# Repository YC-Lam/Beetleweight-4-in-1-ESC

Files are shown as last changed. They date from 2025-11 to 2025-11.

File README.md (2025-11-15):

# beetleweight 4 in 1 brushless ESC
 a 4 in 1 ESC designed for UK beetleweight robots. It can power two brushless drive and one weapon motor.

## Features
- Two 20A brushless drive motor
- Single 80A brushless weapon motor
- Integrated fuse to accommodate BBB rules
- On-board gyroscope to invert controls when bot is inverted (optional)
- On-board BLE reciever to control bot over an XBox controller
- Supports 2-6s Lipo battery
- configurable UVLO, OVP and OCP
- Compact with a 50x50mm dimension
- Single side SMD soldering for easy manufaturing (some hand soldered resistors at the back)

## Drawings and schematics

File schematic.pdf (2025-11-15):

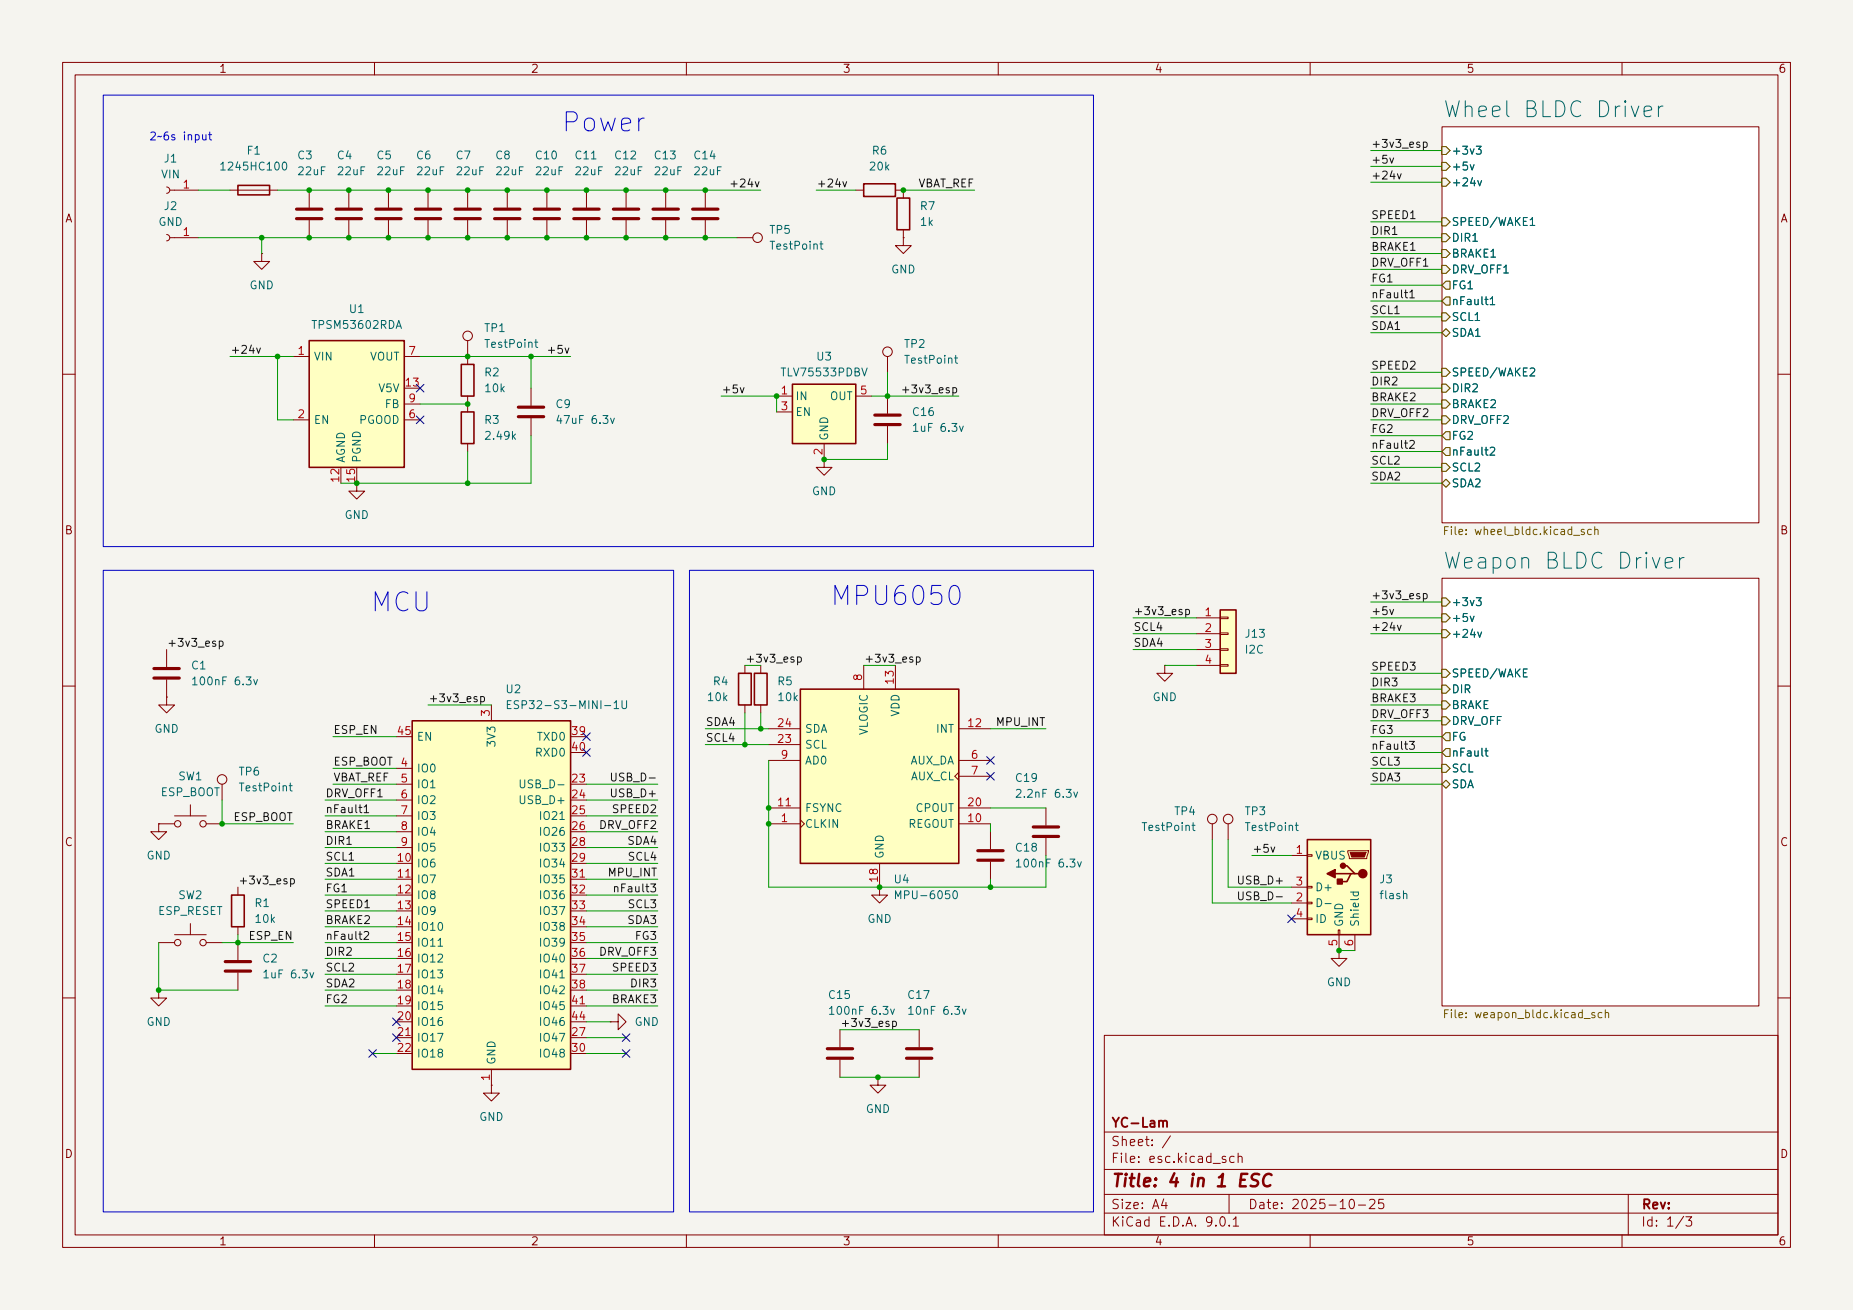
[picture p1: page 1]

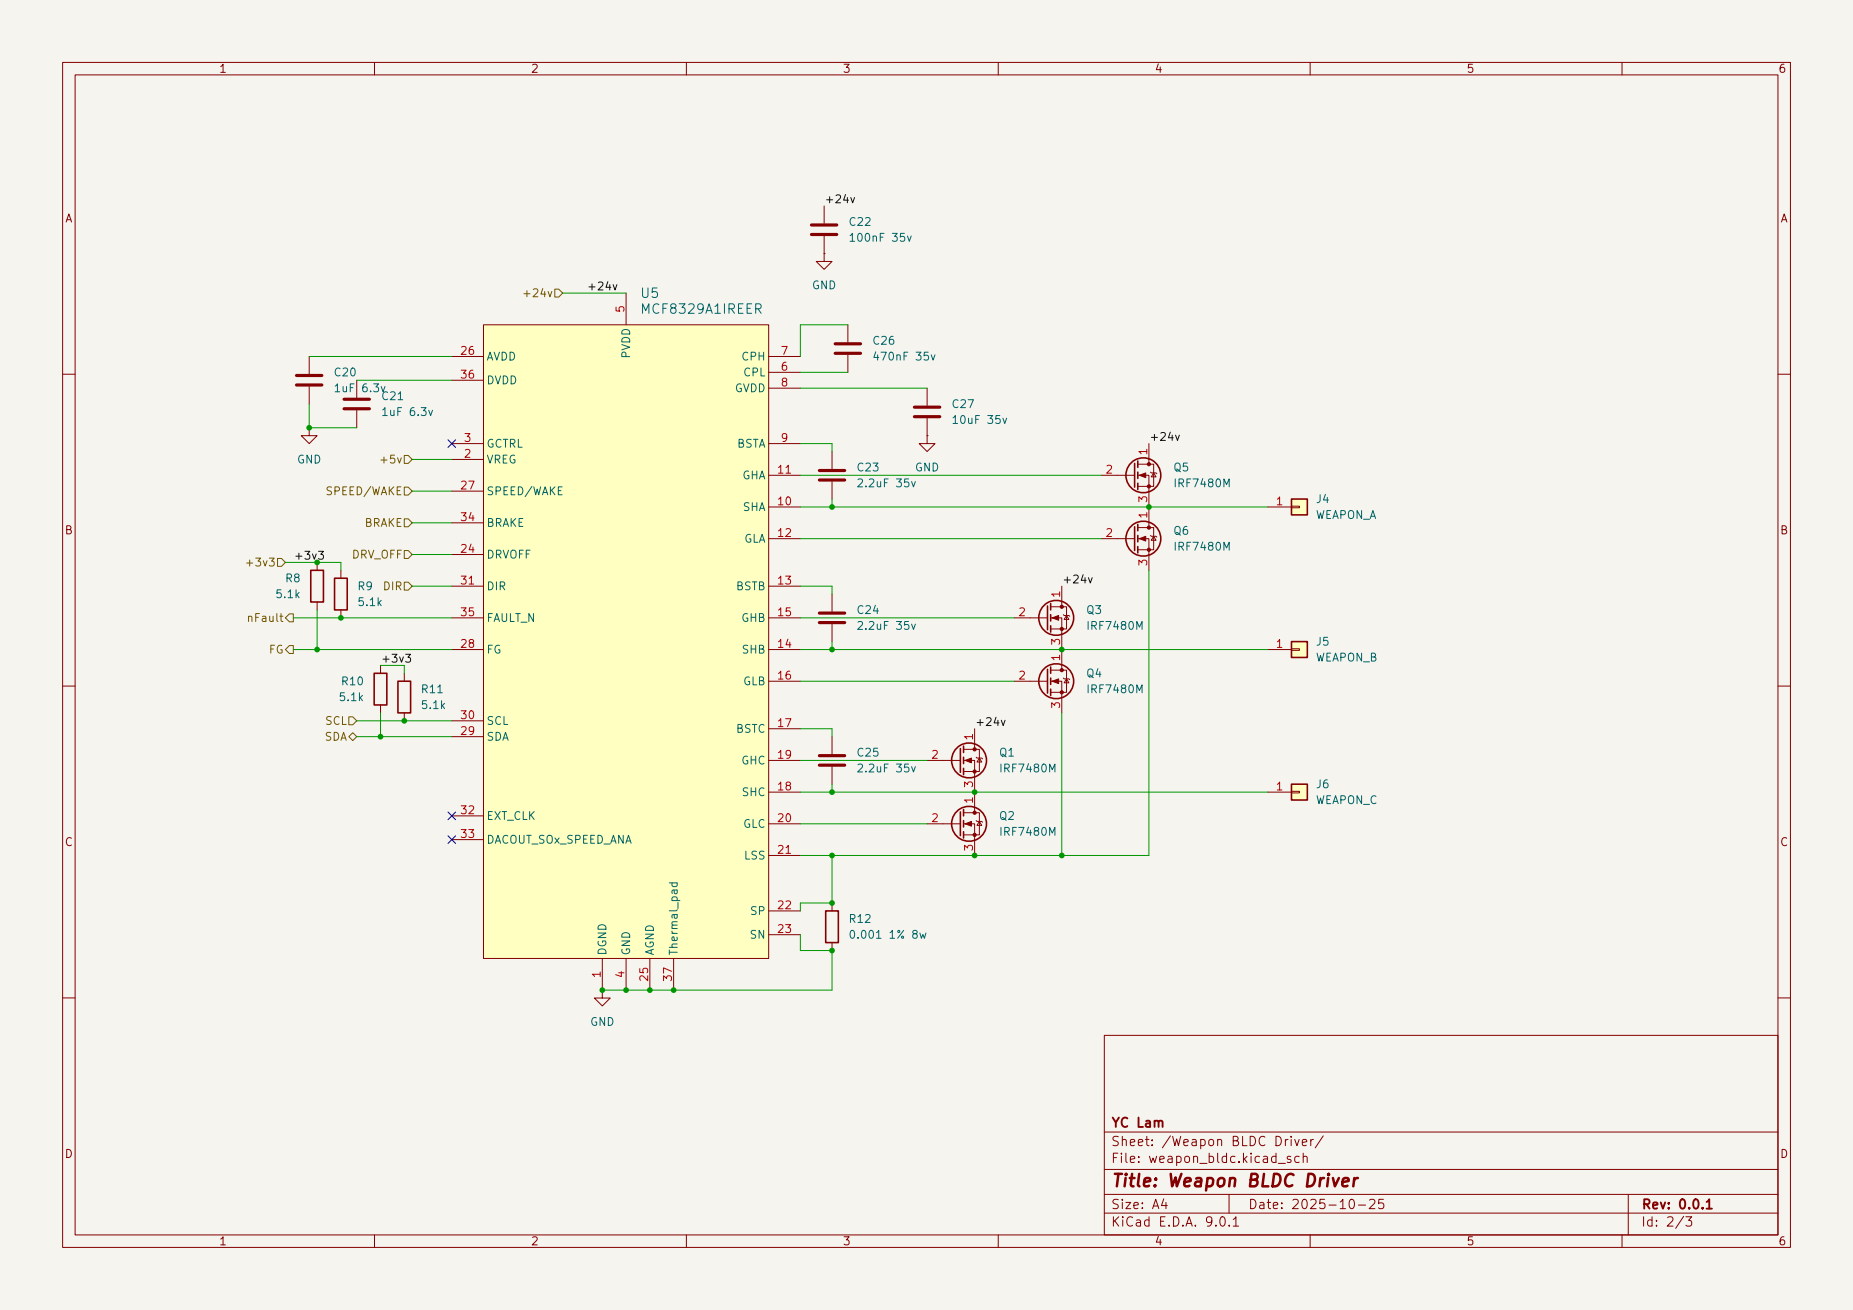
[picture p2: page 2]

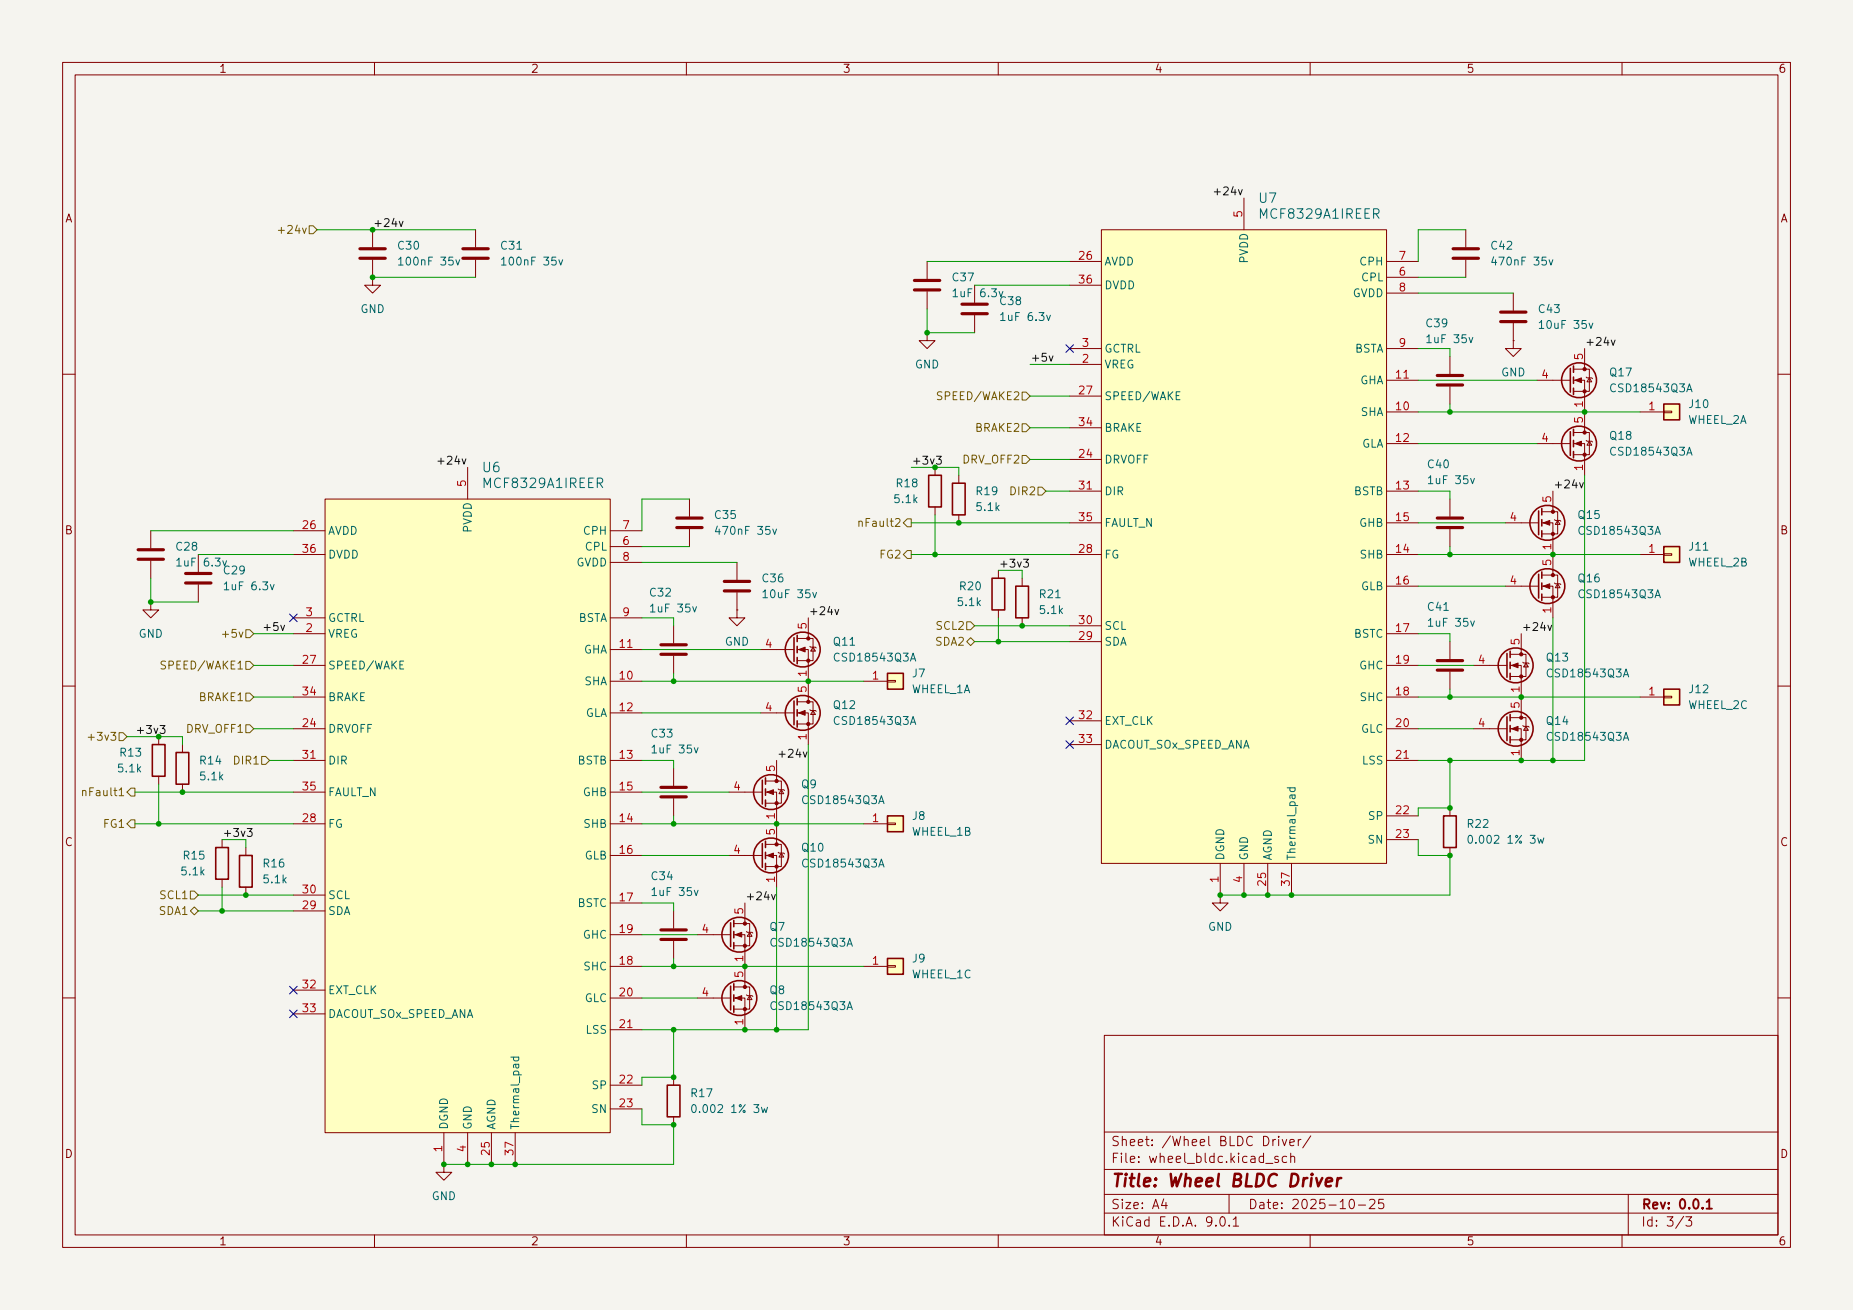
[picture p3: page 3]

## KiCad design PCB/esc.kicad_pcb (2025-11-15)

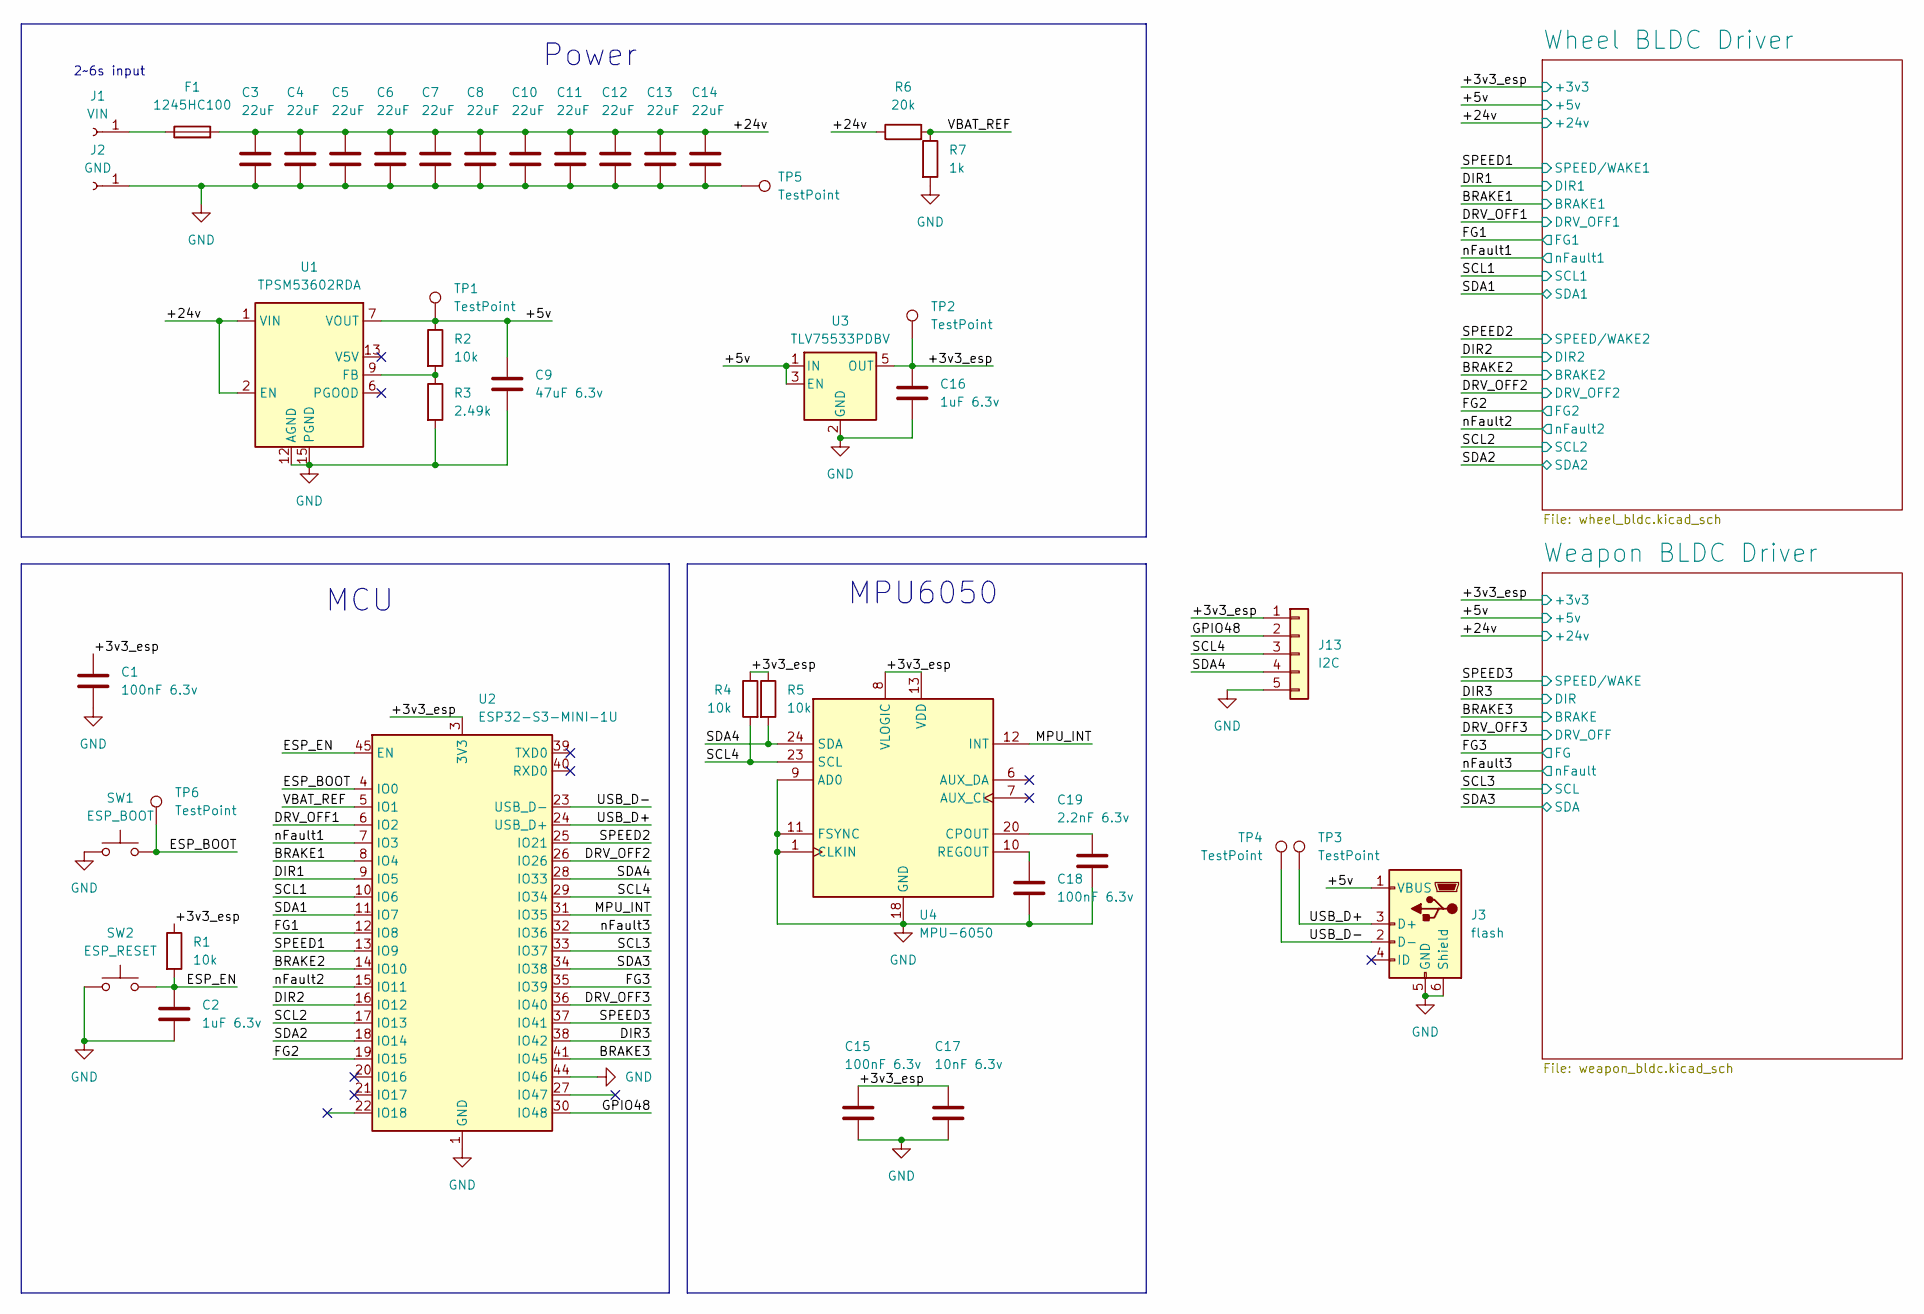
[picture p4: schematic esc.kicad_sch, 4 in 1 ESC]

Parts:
C1, C15, C18: 100nF 6.3v; C_0402_1005Metric
C2: 1uF 6.3v; C_0603_1608Metric_Pad1.08x0.95mm_HandSolder
C3, C4, C5, C6, C7, C8, C10, C11, C12, C13, C14: 22uF; C_0805_2012Metric
C9: 47uF 6.3v; C_0603_1608Metric
C16: 1uF 6.3v; C_0402_1005Metric
C17: 10nF 6.3v; C_0402_1005Metric
C19: 2.2nF 6.3v; C_0402_1005Metric
F1: 1245HC100; 1245HC
J1: VIN; WIRE
J2: GND; WIRE
J3: flash; USB_Micro-B_Molex_47346-0001
J13: I2C; signal wire
R1: 10k; R_0603_1608Metric_Pad0.98x0.95mm_HandSolder
R2, R4, R5: 10k; R_0402_1005Metric
R3: 2.49k; R_0402_1005Metric
R6: 20k; R_0402_1005Metric
R7: 1k; R_0402_1005Metric
SW1: ESP_BOOT; SW_SPST_B3U-1000P
SW2: ESP_RESET; SW_SPST_B3U-1000P
TP1, TP2, TP3, TP4, TP5, TP6: TestPoint; TestPoint_Pad_D1.0mm
U1: TPSM53602RDA; Texas_B3QFN-14-1EP_5x5.5mm_P0.65mm
U2: ESP32-S3-MINI-1U; ESP32-S2-MINI-1U
U3: TLV75533PDBV; SOT-23-5
U4: MPU-6050; InvenSense_QFN-24_4x4mm_P0.5mm

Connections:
/+3v3_esp: C1.1, C15.1, C16.1, C17.1, J13.1, R1.1, R4.1, R5.1, TP2.1, U2.3 (3V3), U3.5 (OUT), U4.8 (VLOGIC), U4.13 (VDD); also elsewhere on the board
/+5v: C9.1, J3.1 (VBUS), R2.1, TP1.1, U1.7 (VOUT), U1.8 (VOUT), U3.1 (IN), U3.3 (EN); also elsewhere on the board
/+24v: C3.1, C4.1, C5.1, C6.1, C7.1, C8.1, C10.1, C11.1, C12.1, C13.1, C14.1, F1.2, R6.1, U1.1 (VIN), U1.2 (EN), U1.14 (VIN); also elsewhere on the board
/BRAKE1: U2.8 (IO4); also elsewhere on the board
/BRAKE2: U2.14 (IO10); also elsewhere on the board
/BRAKE3: U2.41 (IO45); also elsewhere on the board
/DIR1: U2.9 (IO5); also elsewhere on the board
/DIR2: U2.16 (IO12); also elsewhere on the board
/DIR3: U2.38 (IO42); also elsewhere on the board
/DRV_OFF1: U2.6 (IO2); also elsewhere on the board
/DRV_OFF2: U2.26 (IO26); also elsewhere on the board
/DRV_OFF3: U2.36 (IO40); also elsewhere on the board
/ESP_BOOT: SW1.2, TP6.1, U2.4 (IO0)
/ESP_EN: C2.1, R1.2, SW2.2, U2.45 (EN)
/FG1: U2.12 (IO8); also elsewhere on the board
/FG2: U2.19 (IO15); also elsewhere on the board
/FG3: U2.35 (IO39); also elsewhere on the board
/GPIO48: J13.2, U2.30 (IO48)
/MPU_INT: U2.31 (IO35), U4.12 (INT)
/SCL1: U2.10 (IO6); also elsewhere on the board
/SCL2: U2.17 (IO13); also elsewhere on the board
/SCL3: U2.33 (IO37); also elsewhere on the board
/SCL4: J13.3, R4.2, U2.29 (IO34), U4.23 (SCL)
/SDA1: U2.11 (IO7); also elsewhere on the board
/SDA2: U2.18 (IO14); also elsewhere on the board
/SDA3: U2.34 (IO38); also elsewhere on the board
/SDA4: J13.4, R5.2, U2.28 (IO33), U4.24 (SDA)
/SPEED1: U2.13 (IO9); also elsewhere on the board
/SPEED2: U2.25 (IO21); also elsewhere on the board
/SPEED3: U2.37 (IO41); also elsewhere on the board
/USB_D+: J3.3 (D+), TP3.1, U2.24 (USB_D+)
/USB_D-: J3.2 (D-), TP4.1, U2.23 (USB_D-)
/VBAT_REF: R6.2, R7.1, U2.5 (IO1)
/nFault1: U2.7 (IO3); also elsewhere on the board
/nFault2: U2.15 (IO11); also elsewhere on the board
/nFault3: U2.32 (IO36); also elsewhere on the board
GND: C1.2, C2.2, C3.2, C4.2, C5.2, C6.2, C7.2, C8.2, C9.2, C10.2, C11.2, C12.2, C13.2, C14.2, C15.2, C16.2, C17.2, C18.2, C19.2, J2.1, J3.5 (GND), J3.6 (Shield), J13.5, R3.2, R7.2, SW1.1, SW2.1, TP5.1, U1.3 (PGND), U1.10 (PGND), U1.11 (PGND), U1.12 (AGND), U1.15 (PGND), U2.1 (GND), U2.2 (GND), U2.42 (GND), U2.43 (GND), U2.44 (IO46), U2.46 (GND), U2.47 (GND), U2.48 (GND), U2.49 (GND), U2.50 (GND), U2.51 (GND), U2.52 (GND), U2.53 (GND), U2.54 (GND), U2.55 (GND), U2.56 (GND), U2.57 (GND), U2.58 (GND), U2.59 (GND), U2.60 (GND), U2.61 (GND), U2.62 (GND), U2.63 (GND), U2.64 (GND), U2.65 (GND), U3.2 (GND), U4.1 (CLKIN), U4.9 (AD0), U4.11 (FSYNC), U4.18 (GND); also elsewhere on the board
unnamed: F1.1, J1.1
unnamed: R2.2, R3.1, U1.9 (FB)
unnamed: C19.1, U4.20 (CPOUT)
unnamed: C18.1, U4.10 (REGOUT)

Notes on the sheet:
MPU6050
Power
2~6s input
MCU

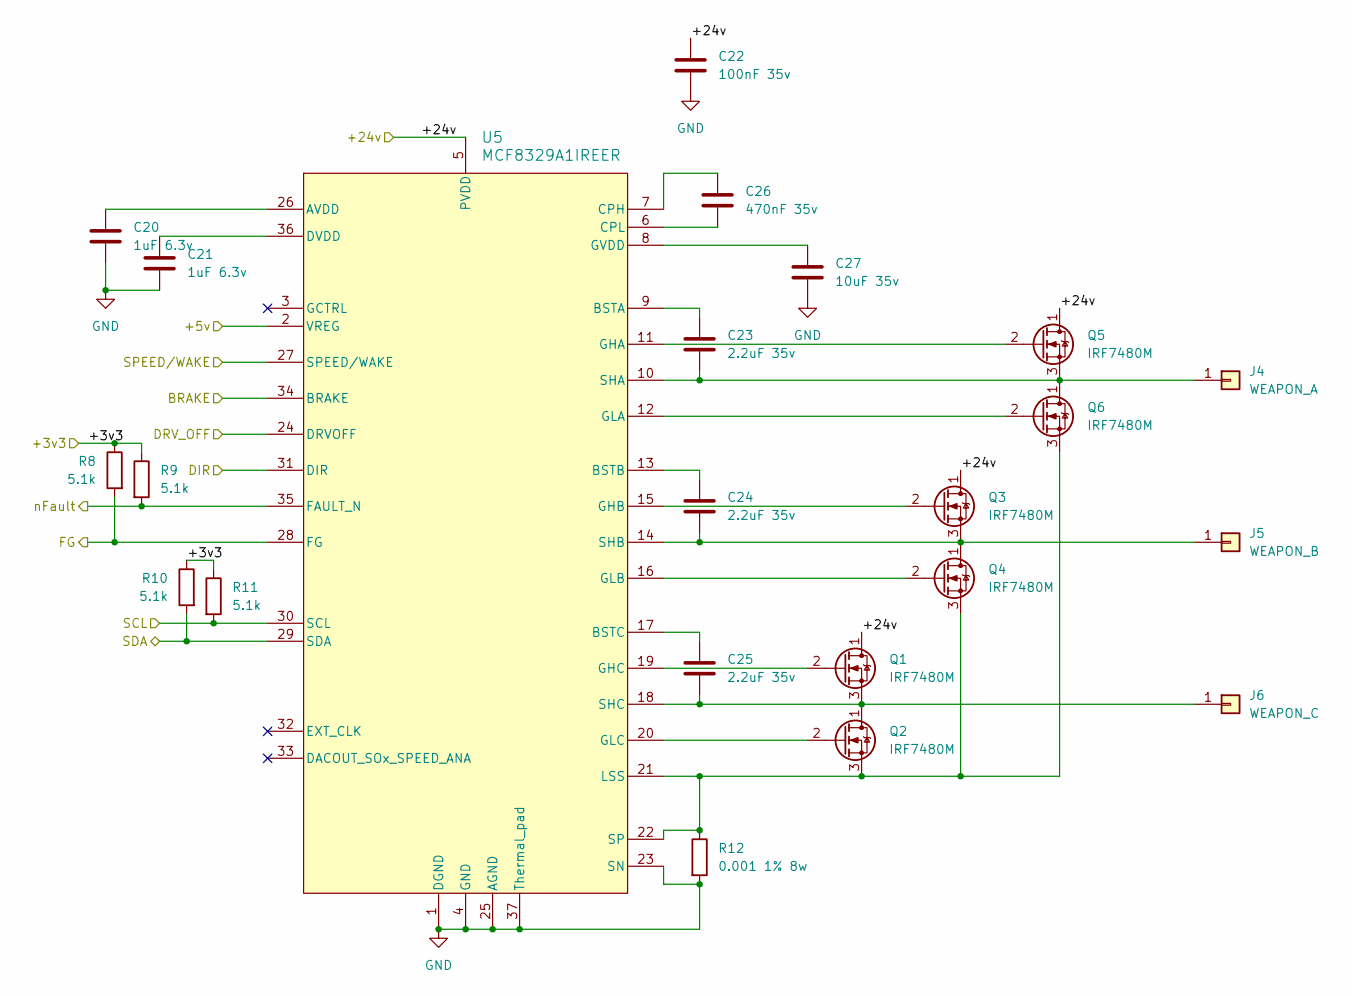
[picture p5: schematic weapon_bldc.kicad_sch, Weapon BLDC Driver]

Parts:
C20, C21: 1uF 6.3v; C_0402_1005Metric
C22: 100nF 35v; C_0402_1005Metric
C23, C24, C25: 2.2uF 35v; C_0402_1005Metric
C26: 470nF 35v; C_0402_1005Metric
C27: 10uF 35v; C_0603_1608Metric
J4: WEAPON_A; WIRE
J5: WEAPON_B; WIRE
J6: WEAPON_C; WIRE
Q1, Q2, Q3, Q4, Q5, Q6: IRF7480M; DirectFET_ME
R8, R9, R10, R11: 5.1k; R_0402_1005Metric
R12: 0.001 1% 8w; R_2512_6332Metric
U5: MCF8329A1IREER; REE0036A-IPC_A

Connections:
/+3v3_esp: R8.1, R9.1, R10.1, R11.1; also elsewhere on the board
/+5v: U5.2 (VREG); also elsewhere on the board
/+24v: C22.1, Q1.1 (D), Q3.1 (D), Q5.1 (D), U5.5 (PVDD); also elsewhere on the board
/BRAKE3: U5.34 (BRAKE); also elsewhere on the board
/DIR3: U5.31 (DIR); also elsewhere on the board
/DRV_OFF3: U5.24 (DRVOFF); also elsewhere on the board
/FG3: R8.2, U5.28 (FG); also elsewhere on the board
/SCL3: R11.2, U5.30 (SCL); also elsewhere on the board
/SDA3: R10.2, U5.29 (SDA); also elsewhere on the board
/SPEED3: U5.27 (SPEED/WAKE); also elsewhere on the board
/nFault3: R9.2, U5.35 (FAULT_N); also elsewhere on the board
GND: C20.2, C21.2, C22.2, C27.2, R12.2, U5.1 (DGND), U5.4 (GND), U5.23 (SN), U5.25 (AGND), U5.37 (Thermal_pad); also elsewhere on the board
unnamed: C23.2, J4.1, Q5.3 (S), Q6.1 (D), U5.10 (SHA)
unnamed: C24.2, J5.1, Q3.3 (S), Q4.1 (D), U5.14 (SHB)
unnamed: C25.2, J6.1, Q1.3 (S), Q2.1 (D), U5.18 (SHC)
unnamed: Q1.2 (G), U5.19 (GHC)
unnamed: Q2.2 (G), U5.20 (GLC)
unnamed: Q2.3 (S), Q4.3 (S), Q6.3 (S), R12.1, U5.21 (LSS), U5.22 (SP)
unnamed: Q3.2 (G), U5.15 (GHB)
unnamed: Q4.2 (G), U5.16 (GLB)
unnamed: Q5.2 (G), U5.11 (GHA)
unnamed: Q6.2 (G), U5.12 (GLA)
unnamed: C20.1, U5.26 (AVDD)
unnamed: C23.1, U5.9 (BSTA)
unnamed: C24.1, U5.13 (BSTB)
unnamed: C25.1, U5.17 (BSTC)
unnamed: C26.1, U5.7 (CPH)
unnamed: C26.2, U5.6 (CPL)
unnamed: C21.1, U5.36 (DVDD)
unnamed: C27.1, U5.8 (GVDD)

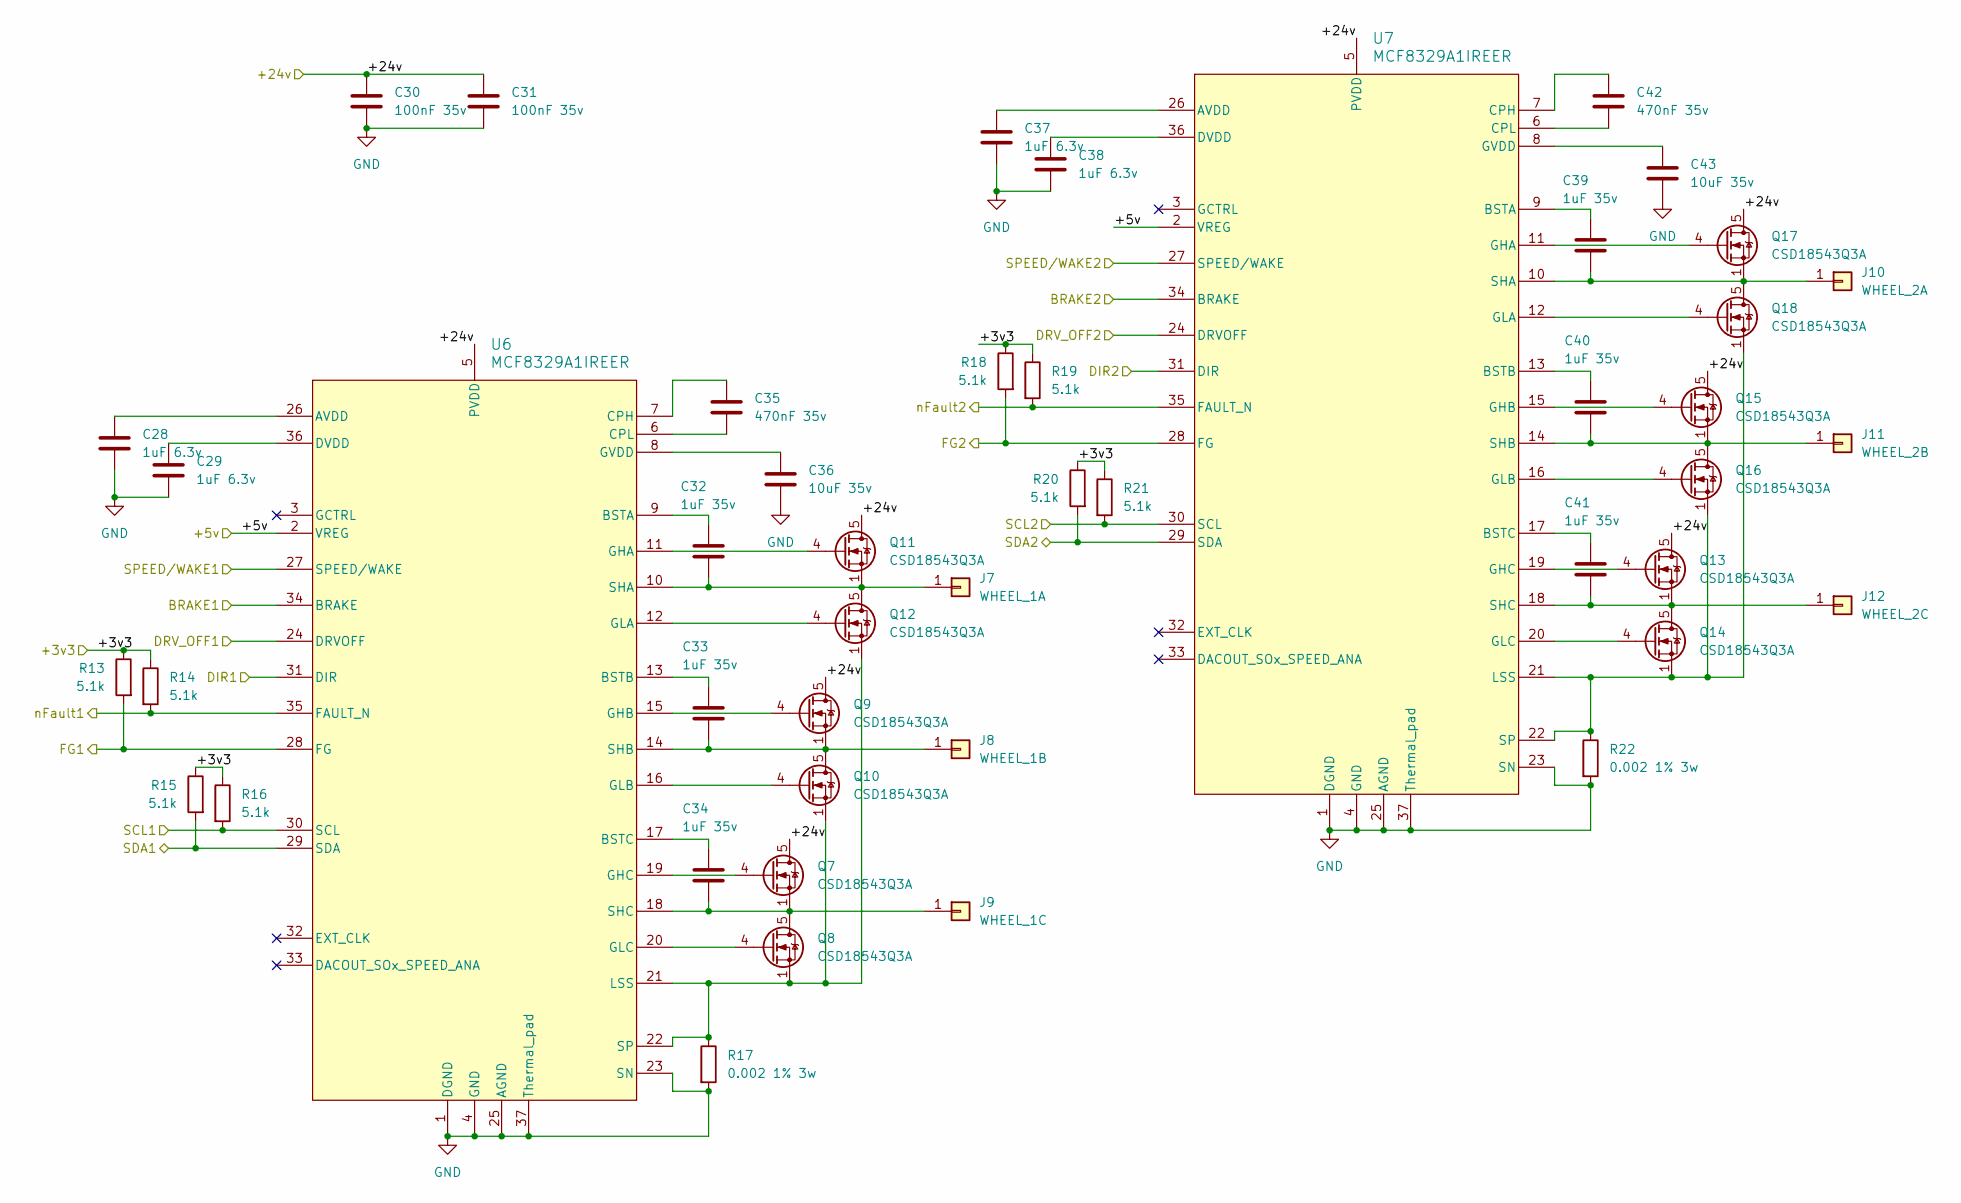
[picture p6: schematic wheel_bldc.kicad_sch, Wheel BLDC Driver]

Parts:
C28, C29, C37, C38: 1uF 6.3v; C_0402_1005Metric
C30, C31: 100nF 35v; C_0402_1005Metric
C32, C33, C34, C39, C40, C41: 1uF 35v; C_0402_1005Metric
C35, C42: 470nF 35v; C_0402_1005Metric
C36, C43: 10uF 35v; C_0603_1608Metric
J7: WHEEL_1A; WIRE
J8: WHEEL_1B; WIRE
J9: WHEEL_1C; WIRE
J10: WHEEL_2A; WIRE
J11: WHEEL_2B; WIRE
J12: WHEEL_2C; WIRE
Q7, Q8, Q9, Q10, Q11, Q12, Q13, Q14, Q15, Q16, Q17, Q18: CSD18543Q3A; VSON-8_3.3x3.3mm_P0.65mm_NexFET
R13, R14, R15, R16, R18, R19, R20, R21: 5.1k; R_0402_1005Metric
R17, R22: 0.002 1% 3w; R_2512_6332Metric
U6, U7: MCF8329A1IREER; REE0036A-IPC_A

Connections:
/+3v3_esp: R13.1, R14.1, R15.1, R16.1, R18.1, R19.1, R20.1, R21.1; also elsewhere on the board
/+5v: U6.2 (VREG), U7.2 (VREG); also elsewhere on the board
/+24v: C30.1, C31.1, Q7.5 (D), Q9.5 (D), Q11.5 (D), Q13.5 (D), Q15.5 (D), Q17.5 (D), U6.5 (PVDD), U7.5 (PVDD); also elsewhere on the board
/BRAKE1: U6.34 (BRAKE); also elsewhere on the board
/BRAKE2: U7.34 (BRAKE); also elsewhere on the board
/DIR1: U6.31 (DIR); also elsewhere on the board
/DIR2: U7.31 (DIR); also elsewhere on the board
/DRV_OFF1: U6.24 (DRVOFF); also elsewhere on the board
/DRV_OFF2: U7.24 (DRVOFF); also elsewhere on the board
/FG1: R13.2, U6.28 (FG); also elsewhere on the board
/FG2: R18.2, U7.28 (FG); also elsewhere on the board
/SCL1: R16.2, U6.30 (SCL); also elsewhere on the board
/SCL2: R21.2, U7.30 (SCL); also elsewhere on the board
/SDA1: R15.2, U6.29 (SDA); also elsewhere on the board
/SDA2: R20.2, U7.29 (SDA); also elsewhere on the board
/SPEED1: U6.27 (SPEED/WAKE); also elsewhere on the board
/SPEED2: U7.27 (SPEED/WAKE); also elsewhere on the board
/nFault1: R14.2, U6.35 (FAULT_N); also elsewhere on the board
/nFault2: R19.2, U7.35 (FAULT_N); also elsewhere on the board
GND: C28.2, C29.2, C30.2, C31.2, C36.2, C37.2, C38.2, C43.2, R17.2, R22.2, U6.1 (DGND), U6.4 (GND), U6.23 (SN), U6.25 (AGND), U6.37 (Thermal_pad), U7.1 (DGND), U7.4 (GND), U7.23 (SN), U7.25 (AGND), U7.37 (Thermal_pad); also elsewhere on the board
unnamed: C32.2, J7.1, Q11.1 (S), Q11.2 (S), Q11.3 (S), Q12.5 (D), U6.10 (SHA)
unnamed: C33.2, J8.1, Q9.1 (S), Q9.2 (S), Q9.3 (S), Q10.5 (D), U6.14 (SHB)
unnamed: C34.2, J9.1, Q7.1 (S), Q7.2 (S), Q7.3 (S), Q8.5 (D), U6.18 (SHC)
unnamed: C39.2, J10.1, Q17.1 (S), Q17.2 (S), Q17.3 (S), Q18.5 (D), U7.10 (SHA)
unnamed: C40.2, J11.1, Q15.1 (S), Q15.2 (S), Q15.3 (S), Q16.5 (D), U7.14 (SHB)
unnamed: C41.2, J12.1, Q13.1 (S), Q13.2 (S), Q13.3 (S), Q14.5 (D), U7.18 (SHC)
unnamed: Q7.4 (G), U6.19 (GHC)
unnamed: Q8.4 (G), U6.20 (GLC)
unnamed: Q9.4 (G), U6.15 (GHB)
unnamed: Q10.4 (G), U6.16 (GLB)
unnamed: Q11.4 (G), U6.11 (GHA)
unnamed: Q12.4 (G), U6.12 (GLA)
unnamed: Q13.4 (G), U7.19 (GHC)
unnamed: Q14.4 (G), U7.20 (GLC)
unnamed: Q15.4 (G), U7.15 (GHB)
unnamed: Q16.4 (G), U7.16 (GLB)
unnamed: Q17.4 (G), U7.11 (GHA)
unnamed: Q18.4 (G), U7.12 (GLA)
unnamed: C28.1, U6.26 (AVDD)
unnamed: C32.1, U6.9 (BSTA)
unnamed: C33.1, U6.13 (BSTB)
unnamed: C34.1, U6.17 (BSTC)
unnamed: C35.1, U6.7 (CPH)
unnamed: C35.2, U6.6 (CPL)
unnamed: C29.1, U6.36 (DVDD)
unnamed: C36.1, U6.8 (GVDD)
unnamed: Q8.1 (S), Q8.2 (S), Q8.3 (S), Q10.1 (S), Q10.2 (S), Q10.3 (S), Q12.1 (S), Q12.2 (S), Q12.3 (S), R17.1, U6.21 (LSS), U6.22 (SP)
unnamed: C37.1, U7.26 (AVDD)
unnamed: C39.1, U7.9 (BSTA)
unnamed: C40.1, U7.13 (BSTB)
unnamed: C41.1, U7.17 (BSTC)
unnamed: C42.1, U7.7 (CPH)
unnamed: C42.2, U7.6 (CPL)
unnamed: C38.1, U7.36 (DVDD)
unnamed: C43.1, U7.8 (GVDD)
unnamed: Q14.1 (S), Q14.2 (S), Q14.3 (S), Q16.1 (S), Q16.2 (S), Q16.3 (S), Q18.1 (S), Q18.2 (S), Q18.3 (S), R22.1, U7.21 (LSS), U7.22 (SP)

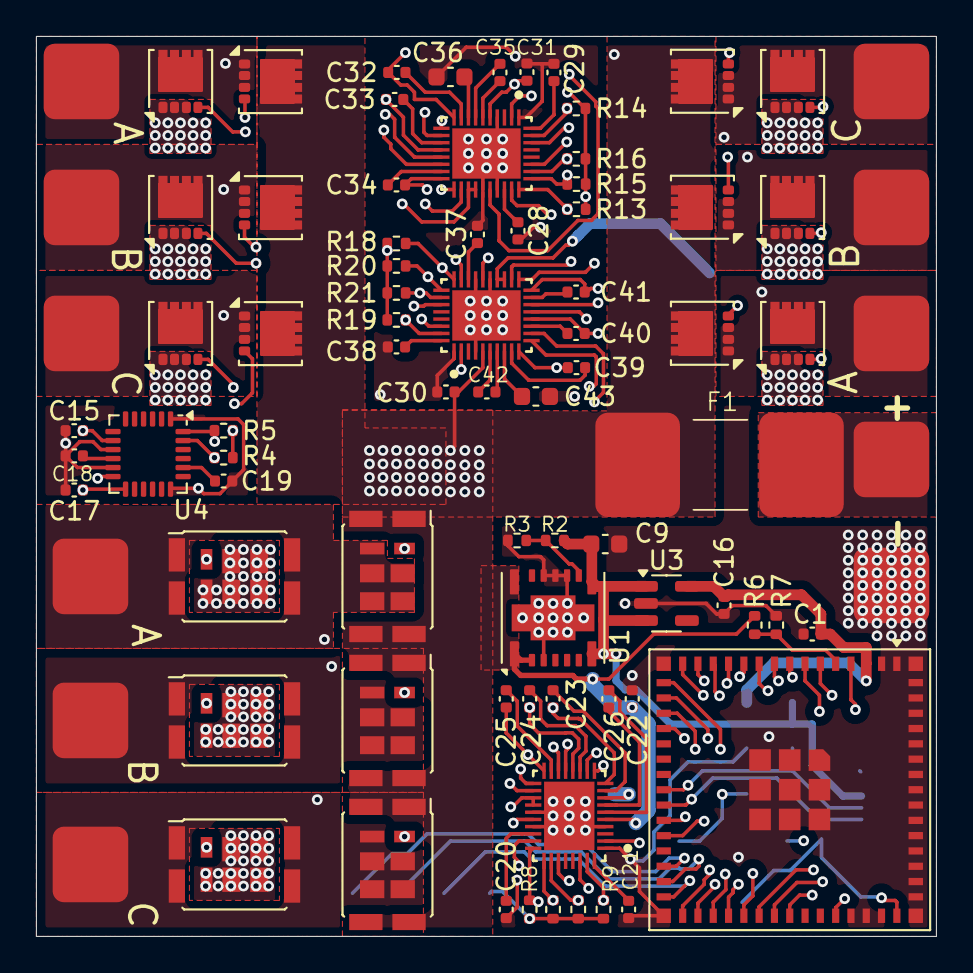
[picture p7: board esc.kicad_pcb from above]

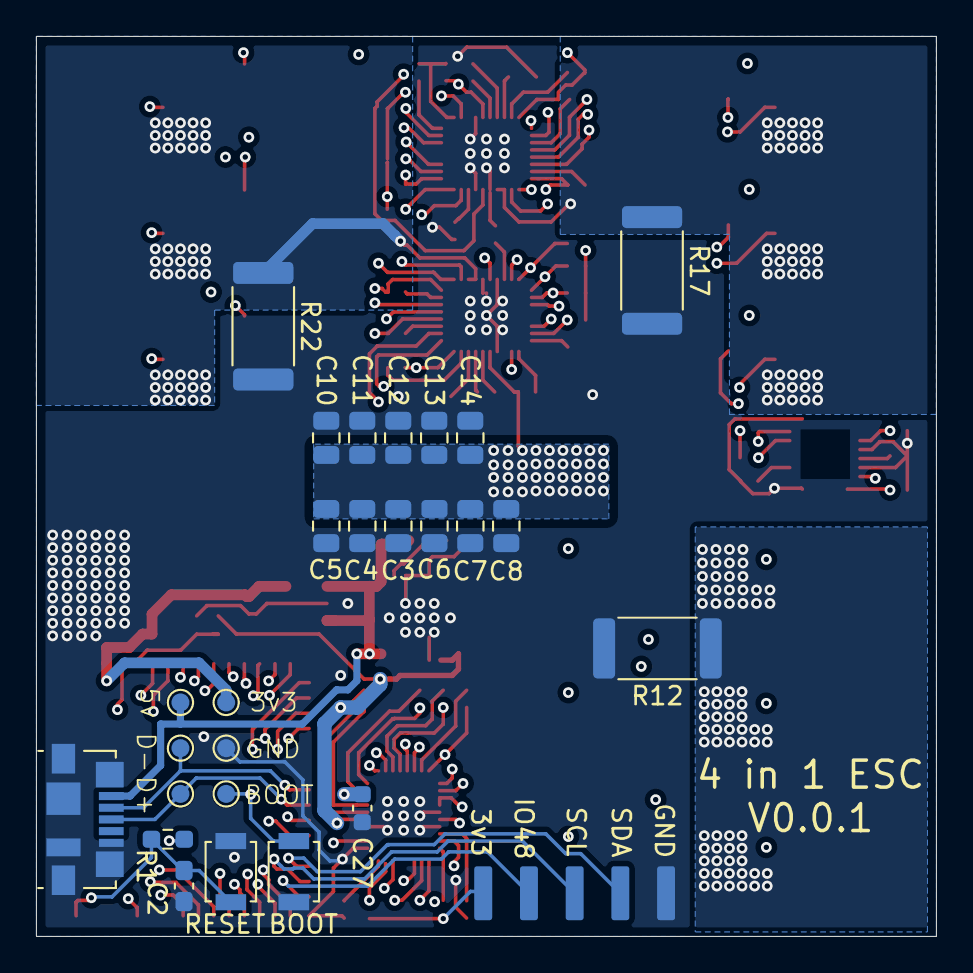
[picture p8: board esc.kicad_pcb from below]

Board: 4 copper layers, 50.0 x 50.0 mm, 112 parts (27 on the bottom side), 95 nets.
